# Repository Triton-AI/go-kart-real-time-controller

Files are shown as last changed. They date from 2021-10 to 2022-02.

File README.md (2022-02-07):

# Go-Kart Real-Time Controller



## Navigation

This repository is organized as follows:

- `ROS2` contains the gokart packet library and ROS2 driver
- `PCB` contains Altium PCB design files
- `MCU` contains microcontroller codes ([depricated, moved to a separate repository](https://github.com/Triton-AI/go-kart-real-time-controller-mbed))

## Documentations

- [Getting started with packet communication library](ROS2/src/tai_gokart_packet/design/README.md)
- [Packet API documentation](ROS2/src/tai_gokart_packet/design/Packet_API.md)

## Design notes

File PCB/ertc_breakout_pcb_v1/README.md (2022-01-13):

# V1 Errors
NUCLEO Connectors (J1, J2) flipped pinout

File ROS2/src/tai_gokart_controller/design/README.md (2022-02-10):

# Go Kart Controller - ROS2 Driver

## Purpose of Package

This packet is a ROS2 driver for Triton AI's go-kart real-time controller. The current development work targets ROS2 Galactic.

The packet is capable of sending control messages and receive sensor and state report from the controller.

## API

## Inner Working

The packet assumes the following state machine exists on the MCU. See a detailed explanation in the [MCU code repository](https://github.com/Triton-AI/go-kart-real-time-controller-mbed).

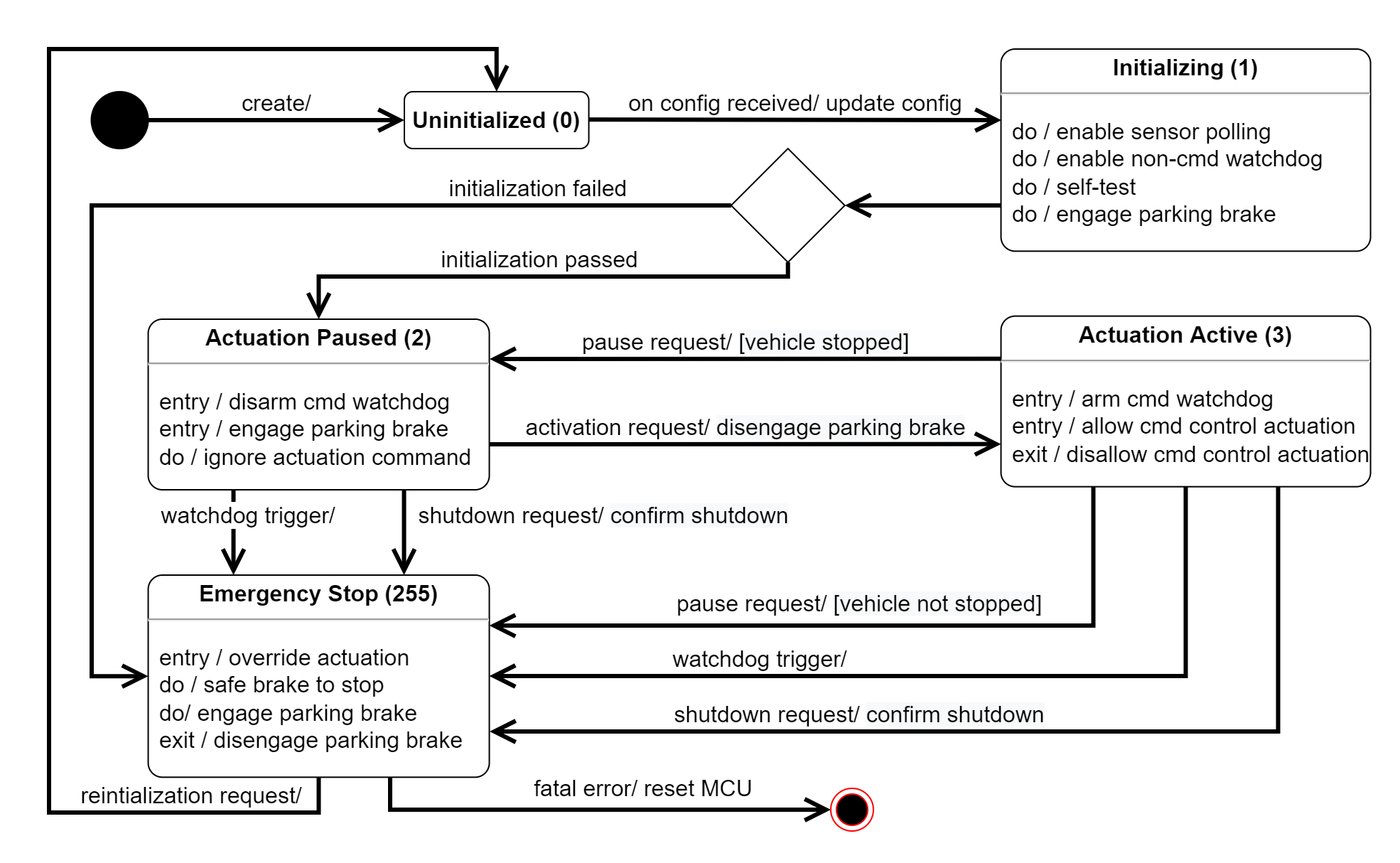
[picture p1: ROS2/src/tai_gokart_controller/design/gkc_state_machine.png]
GKC State Machine


The state machine proposal is purposefully made close to [ROS2 Lifecycle](https://design.ros2.org/articles/node_lifecycle.html) to enable easier management, with the major difference being an additional "emergency stop" state. Since ROS2 Lifecycle system does not support custom state, it is implemented as part of the uninitialized state in ROS2 Lifecycle, while the error state is used to direct all emergency stop requests to the uninitialized state.

Another difference is in the shutdown procedure where shutdown transition will always eventually end in emergency stop state (by signaling transition error and be directed to uninitialized state). The rationale is that the software should always have control or communication with the vehicle as much as possible, instead of destructing such interface. Only fatal error or user interrupt can destruct the node.

## Known Issues

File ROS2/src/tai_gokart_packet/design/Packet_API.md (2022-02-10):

# Packet API

## Introduction

The transfer of messages through network interfaces of the team's choice (Serial, CAN, Ethernet) follows a standardized packet API for message serialization (encoding) and deserialization (decoding).

The low-level communication interface (LLCI) of Serial, CAN and Ethernet is agnostic about what is being transferred. On top of that, the high-level communication interface (HLCI), which is mainly the packet factory, is responsible for encoding and decoding between C++ class representation of message and low-level buffer to/from LLCI.

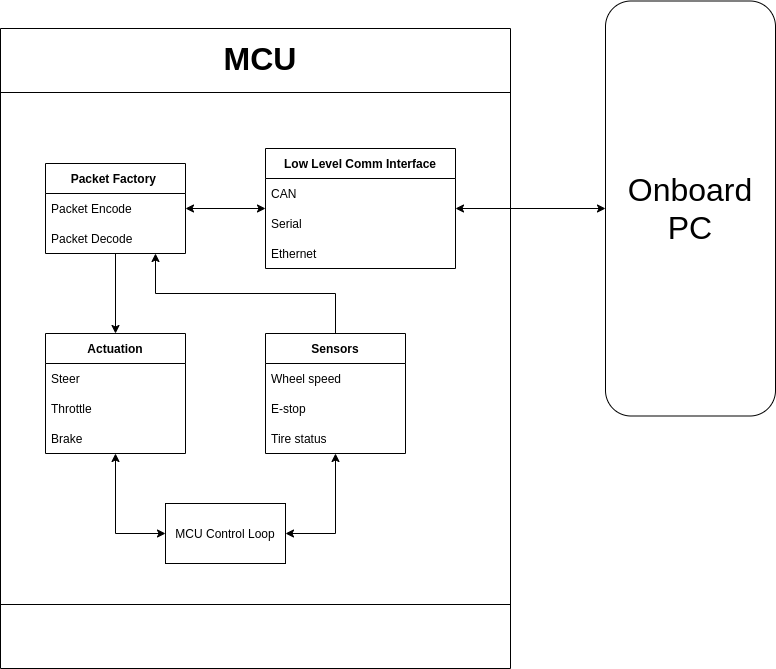
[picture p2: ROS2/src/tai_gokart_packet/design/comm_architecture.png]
Communication Architecture


There are packet factories on both sides of the communication system, making it a reusable common library for both Go-Kart Controller (GKC) software and high-level softwares (ROS2).

## Packet Basics

Each packet is a variable buffer of bytes.

The Packet API takes substantial reference from VESC packet API.

A standard packet begins with byte 0x02, followed by 1 byte of payload length. Payload cannot exceed 256 bytes. After that, 2 bytes are used for payload checksum, and finally there is one termination byte 0x03.

The **first byte (FB)** of each payload type is uniquely identifiable.

Extended packet is not needed and not implemented at the moment, but any LLCI implementation should not rule out the possibility of such packet in the future.

To avoid garbage data, unused payload buffer section should be initiated to 0x00. 0x00 cannot have any substaintial meaning in the playload other than data.

## Core Payloads

These messages concerns the basic communication and device control, such as communication establishment, firmware version, MCU reset, heartbeat, and watchdog.

### Handshake \#1

Payload size: 5 Byte

FB: 0x04

The first handshake is initiated by the PC. The first byte of the payload is 0x04, followed by a 4-byte randomly generated unsigned integer as the sequence number.

### Handshake \#2

Payload size: 5 Byte

FB: 0x05

The second handshake given by the MCU after hearing handshake #1 from the PC. The first byte of the payload is 0x05, followed by a 4-byte unsigned integer which is the bit-wise complement of the number in handshake #1.

### Request Firmware Version

Payload size: 1 Byte

FB: 0x06

The PC requesting firmware version from the MCU.

### Respond Firmware Version

Payload size: 4 Byte

FB: 0x07

The MCU's response of firmware version in three `uint8`: version `x.y.z`

### Reset MCU

Payload size: 5 Byte

FB: 0xFF

The PC commanding a MCU reset. the four bytes of the message contains alternating 1s and 0s (decimal 2863311530 or hex AAAAAAAA).

### Heartbeat

Payload size: 3 Byte

FB: 0xAA

Bidirectional message with a `uint8` rolling counter that increments or overflows with every message sent to the other side, as well as a `uint8` state code of the MCU state machine state, which is only sent by MCU.

### Log

Payload size: variable

FB: 0xAD

String log with severity level of info, warning, error or fatal. The `c_str` content of the string cannot exceed 253 byte. The response to different severity levels is implementation-dependant.

## Configuration Payloads

These messages set the configurations of the controller.

### Configuation

Payload size: 49 Byte

FB: 0xA0

The PC sends configuations to the MCU, containing actuation calibrations and watchdog timeout intervals.

## Control Payloads

### Control

Payload size: 13 Byte

FB: 0xAB

The PC commands steering, throttle, and brake to the MCU.

### State Transition

Payload size: 2 Byte

FB: 0xA1

The PC requests a state transition on the MCU. Possible states include unintialized, initialized, active, paused, and emergency stop.

### Shutdown \#1

Payload size: 5 Byte

FB: 0xA2

The PC requests a shutdown to the MCU. The message contains a sequence number.

### Shutdown \#2

Payload size: 5 Byte

FB: 0xA3

The MCU responds to the shutdown command from the computer by adding one to the incoming sequence number in Shutdown #1.

## Feedback Payloads

### Sensors

These messages request or send GKC state, and sensor feedbacks.

Payload size: 48 Byte

FB: 0xAC

The MCU sends sensor data to the PC, containing wheel speeds, pressures, voltage, etc., and sensor fault flags.

## Reference

| Description | Payload size | Payload FB | Data Structure | Sender |
|---|---|---|---|---|
| Handshake #1 | 5 | 0x04 | uint32 sequence number. | PC |
| Handshake #2 | 5 | 0x05 | uint32 sequence number | MCU |
| Request Firmware Version | 1 | 0x06 | | PC |
| Respond Firmware Version | 4 | 0x07 | 3 * uint8 version number | MCU |
| Reset MCU | 5 | 0xFF | uint32 magic number | PC |
| Heartbeat | 2 | 0xAA | uint8 rolling counter | Both |
| Log | Variable | 0xAD | severity and string content | Both |
| Configuration | 49 | 0xA0 | a packed struct of configurables | PC |
| Control | 13 | 0xAB | throttle, steering, and brake | PC |
| State Transition | 2 | 0xA1 | uint8 state number | PC |
| Sensors | 22 | 0xAC | a packed struct of sensor readings | MCU |
| Shutdown \#1 | 5 | 0xA2 | uint32 sequence number. | PC |
| Shutdown \#2 | 5 | 0xA3 | uint32 sequence number. | MCU |

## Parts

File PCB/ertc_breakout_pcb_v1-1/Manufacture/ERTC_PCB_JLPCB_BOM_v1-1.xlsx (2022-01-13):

Part Number | Description | Designator | Footprint | Manufacturer 1 | Manufacturer Part Number 1 | Supplier 1 | Supplier Part Number 1 | Quantity | Comment
CGA3E2X7R1H472K080AA | CAP CER 4700PF 50V X7R 0603 | C1, C3 | CAP 0603_1608 |  |  | DigiKey | 445-5661-1-ND | 2
CL10B104KA8NNNC | CAP CER 0.1UF 25V X7R 0603 | C2, C4, C5, C6, C7, C8, C9 | CAP 0603_1608 |  |  | DigiKey | 1276-1006-1-ND | 7
LTST-C170GKT | LED GREEN CLEAR SMD | D1 | LED 0805_2012 GREEN |  |  | DigiKey | 160-1179-1-ND | 1
SSW-135-01-T-D |  | J1, J2 | SAMTEC_SSW-135-03-G-D |  |  |  |  | 2 | DNP
A-DF_09_A/KG-T2S | 9 Position D-Sub Receptacle, Female Sockets Connector | J3, J4, J7 | ASSMANN_A-DF09A/KG-T2S |  |  |  |  | 3 | DNP
39-30-1039 | Connector Header Through Hole 3 position 0.165 _4.20mm_ | J5, J6, J8, J9, J11, J12, J13, J14, J15, J16, J17, J18, J19, J20, J23, J24, J25 | MOLEX_39-30-1039 |  |  |  |  | 17 | DNP
0039281063 | Connector Header Through Hole, 6 position 0.165 (4.20mm) | J10, J21, J22 | MOLEX_0039281063 |  |  |  |  | 3 | DNP
0039301049 | Connector Header Through Hole 4 position 0.165 _4.20mm_ | J26, J27, J28, J29, J30, J32, J33, J34, J35, J36 | MOLEX_0039301049 |  |  |  |  | 10 | DNP
XT30UPB-M | Plug; DC supply; XT30; male; PIN: 2; for cable; soldered; 30A; 500V | J31 | AMASS_XT30-M |  |  |  |  | 1 | DNP
RNCP0805FTD1K00 | RES 1K OHM 1% 1/4W 0805 | R1, R3, R5, R7 | RES 0805_2012 |  |  | DigiKey | RNCP0805FTD1K00CT-ND | 4 | DNP
RMCF0603FT60R4 | RES 60.4 OHM 1% 1/10W 0603 | R2, R4, R6, R8 | RES 0603_1608 |  |  | DigiKey | RMCF0603FT60R4CT-ND | 4
CRCW06030000Z0EBC | RES SMD 0 OHM JUMP 1/10W 0603 | R9, R11, R12, R13, R14, R15, R16, R17, R18 | RES 0603_1608 |  |  | DigiKey | 541-4013-1-ND | 9 | DNP
CRGCQ0603F1K2 | CRGCQ 0603 1K2 1% | R10 | RES 0603_1608 |  |  | DigiKey | A129689CT-ND | 1
SN65HVD230DR | 3.3 V CAN Transceiver with Standby Mode 8-SOIC -40 to 85 | U1, U2 | SOIC127P599X175-8N |  |  |  |  | 2
MAX3232IDR | 3-V to 5.5-V multichannel RS-232 line driver & receiver 16-SOIC -40 to 85 | U3 | SOIC127P600X175-16N |  |  |  |  | 1

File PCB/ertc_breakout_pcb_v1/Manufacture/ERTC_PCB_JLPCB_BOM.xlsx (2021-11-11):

Part Number | Description | Designator | Footprint | Manufacturer | Manufacturer Part Number 1 | Supplier 1 | Supplier Part Number 1 | Quantity | Comment
CL10B472JB8NNNC | X7R 4.7nF ±5% 50V 0603 Multilayer Ceramic Capacitors MLCC - SMD/SMT ROHS | C1, C3 | CAP 0603_1608 | Murata Electronics |  |  |  | 2
CL10B104JB8NNNC | X7R 100nF ±5% 50V 0603 Multilayer Ceramic Capacitors MLCC - SMD/SMT ROHS | C2, C4, C5, C6, C7, C8, C9 | CAP 0603_1608 | Samsung Electro-Mechanics |  |  |  | 7
LTST-C170GKT | LED GREEN CLEAR SMD | D1 | LED 0805_2012 GREEN | Lite-On Inc. |  | DigiKey | 160-1179-1-ND | 1
SSW-135-01-T-D |  | J1, J2 | SAMTEC_SSW-135-01-T-D | Samtec |  |  |  | 2 | DNP
A-DF_09_A/KG-T2S | 9 Position D-Sub Receptacle, Female Sockets Connector | J3, J4, J7 | ASSMANN_A-DF09A/KG-T2S | Assmann WSW Components |  | Digikey | AE10921-ND | 3 | DNP
39-30-1039 | Connector Header Through Hole 3 position 0.165 _4.20mm_ | J5, J6, J8, J9, J11, J12, J13, J14, J15, J16, J17, J18, J19, J20, J21, J22, J23, J24, J25 | MOLEX_39-30-1039 |  |  |  |  | 19 | DNP
0039281063 | Connector Header Through Hole, 6 position 0.165 (4.20mm) | J10 | MOLEX_0039281063 |  |  |  |  | 1 | DNP
0039301049 | Connector Header Through Hole 4 position 0.165 _4.20mm_ | J26, J27, J28, J29, J30, J32, J33, J34, J35, J36 | MOLEX_0039301049 |  |  |  |  | 10 | DNP
XT30UPB-M | Plug; DC supply; XT60; male; PIN: 2; for cable; soldered; 30A; 500V | J31 | AMASS_XT30-M |  |  |  |  | 1 | DNP
RNCP0805FTD1K00 | 250mW ±1% ±25ppm/℃ 1kΩ - 0805 Chip Resistor - Surface Mount ROHS | R1, R3, R5, R7 | RES 0805_2012 | UNI-ROYAL(Uniroyal Elec) |  |  |  | 4 | DNP
0603WAF604JT5E | 60.4Ω ±1% ±100ppm/℃ 0.1W 0603 Chip Resistor - Surface Mount ROHS | R2, R4, R6, R8 | RES 0603_1608 | UNI-ROYAL(Uniroyal Elec) |  |  |  | 4
CRCW06030000Z0EBC | RES SMD 0 OHM JUMP 1/10W 0603 | R9 | RES 0603_1608 | Vishay Dale |  | DigiKey | 541-4013-1-ND | 1 | DNP
0603WAJ0122T5E | 1.2kΩ ±5% ±100ppm/℃ 0.1W 0603 Chip Resistor - Surface Mount ROHS | R10 | RES 0603_1608 | UNI-ROYAL(Uniroyal Elec) |  |  |  | 1
SN65HVD230DR | 3.3 V CAN Transceiver with Standby Mode 8-SOIC -40 to 85 | U1, U2 | SOIC127P599X175-8N | Texas Instruments |  | DigiKey | 296-11654-2-ND | 2
MAX3232IDR | 3-V to 5.5-V multichannel RS-232 line driver & receiver 16-SOIC -40 to 85 | U3 | SOIC127P600X175-16N | Texas Instruments |  | DigiKey | 296-13098-2-ND | 1

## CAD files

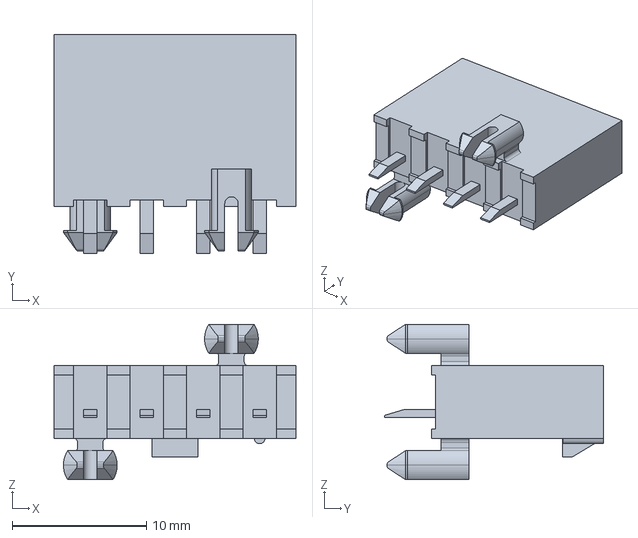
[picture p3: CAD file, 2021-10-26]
PCB/ertc_breakout_pcb_v1-1/CAD Models/0039301049/39-30-1049.stp
18.0 x 16.3 x 11.6 mm

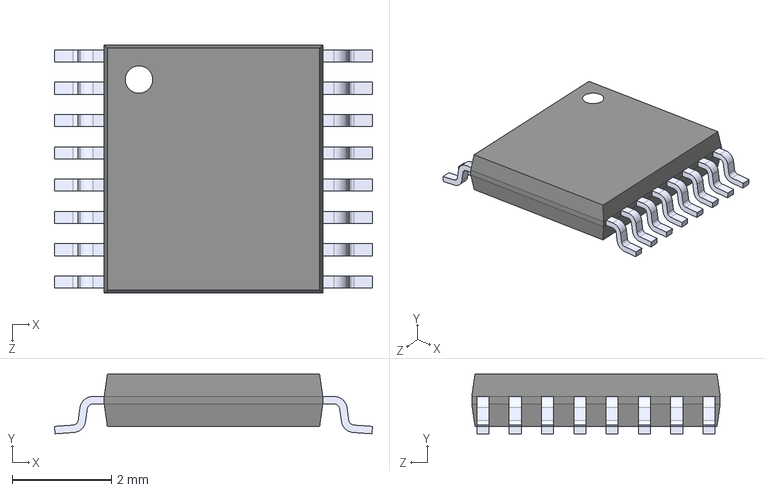
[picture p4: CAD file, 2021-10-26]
PCB/ertc_breakout_pcb_v1-1/CAD Models/MAX3221EIPWR/MAX3221EIPWR.STEP
6.40 x 1.20 x 5.00 mm

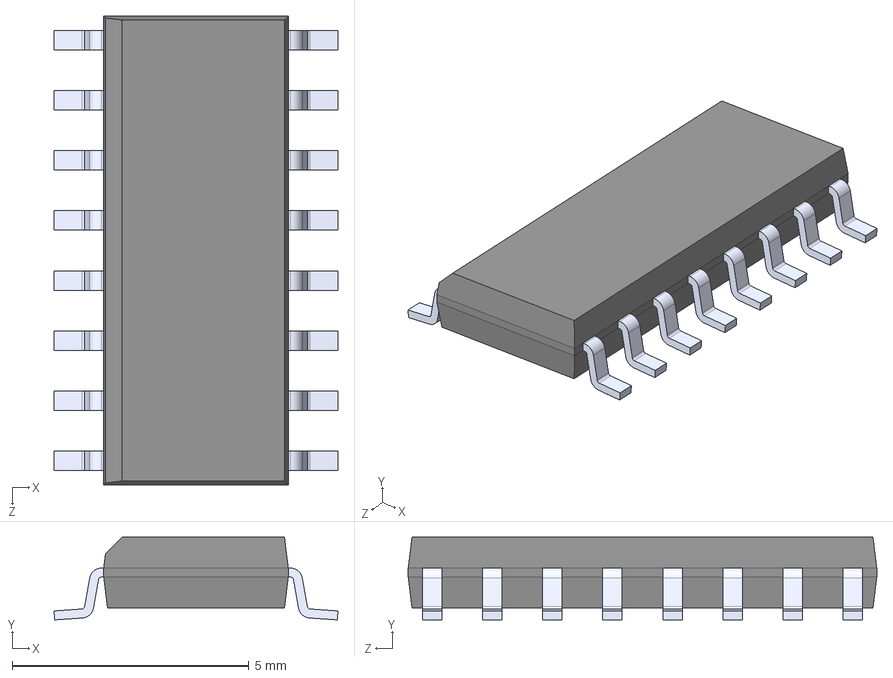
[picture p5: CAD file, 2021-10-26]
PCB/ertc_breakout_pcb_v1-1/CAD Models/MAX3232IDR/MAX3232IDR.STEP
6.00 x 1.75 x 9.90 mm

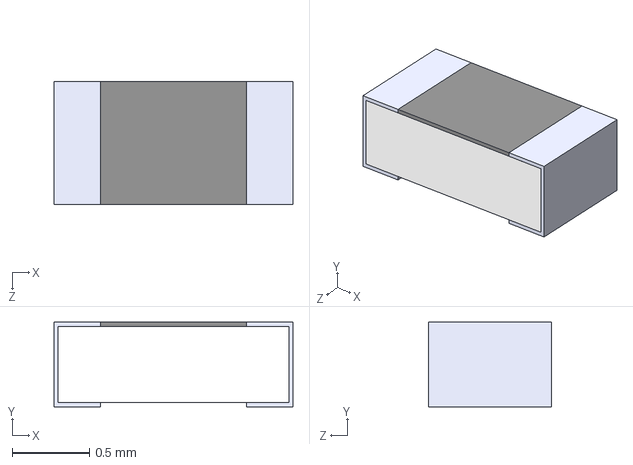
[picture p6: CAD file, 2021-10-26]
PCB/ertc_breakout_pcb_v1-1/CAD Models/RMCF0603FT60R4/RMCF0603FT60R4.STEP
1.55 x 0.55 x 0.8 mm

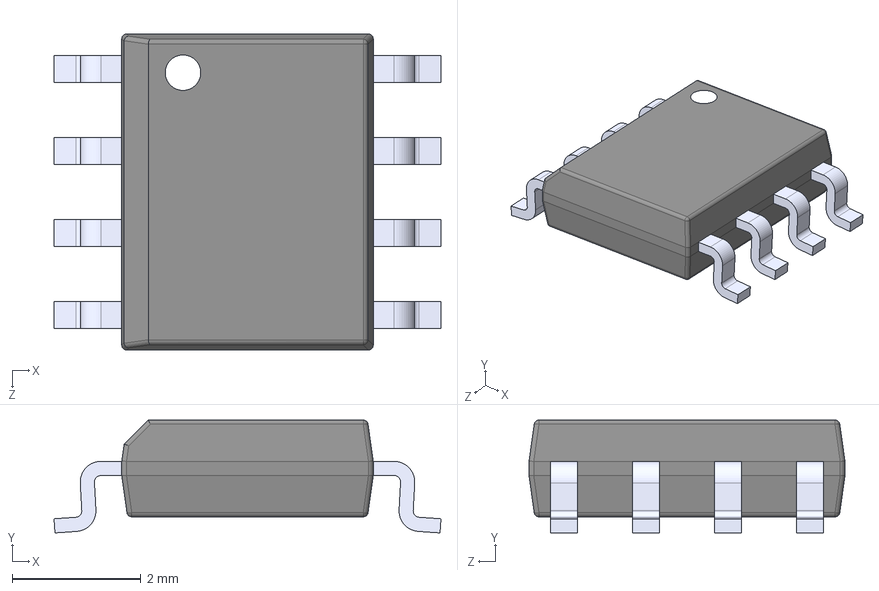
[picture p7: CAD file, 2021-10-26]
PCB/ertc_breakout_pcb_v1-1/CAD Models/SN65HVD230DR/SN65HVD230DR.STEP
6.00 x 1.75 x 4.90 mm

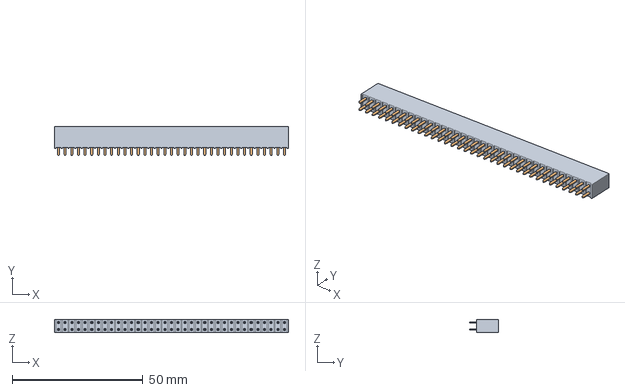
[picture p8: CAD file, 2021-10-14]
PCB/ertc_breakout_pcb_v1-1/CAD Models/SSW-135-01-T-D/SSW-135-01-T-D.stp
89.4 x 11.2 x 4.95 mm
_T1SSW-135-01-T-D
_P2SSW-135-01-T-D

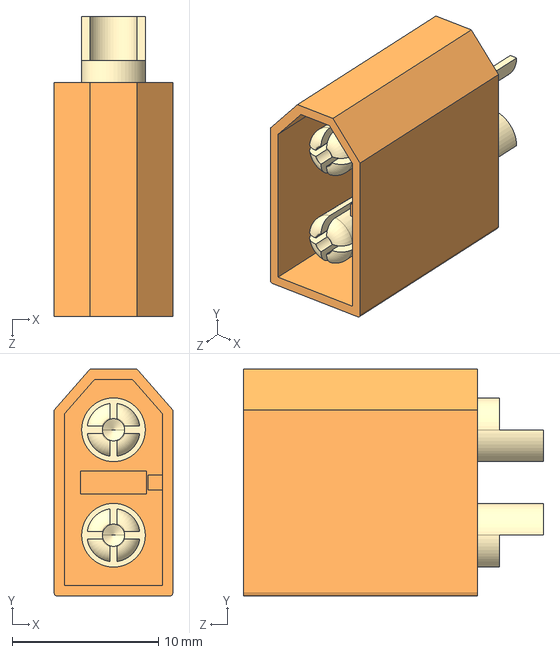
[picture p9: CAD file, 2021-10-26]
PCB/ertc_breakout_pcb_v1-1/CAD Models/XT60-M/XT60-M--3DModel-STEP-56544.STEP
8.10 x 15.5 x 20.5 mm

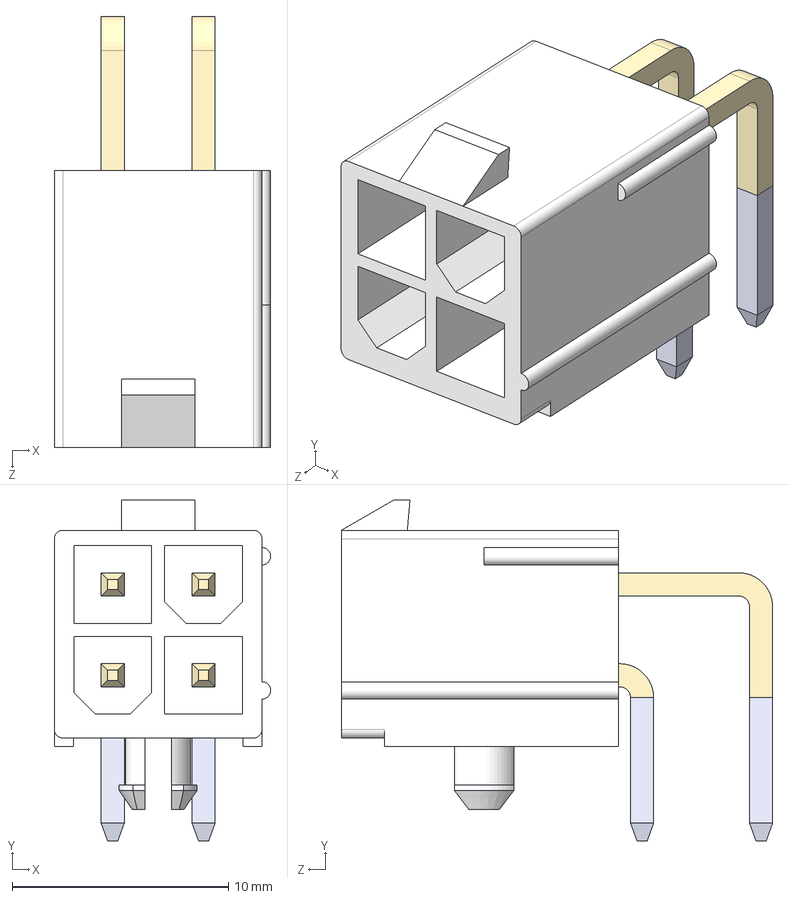
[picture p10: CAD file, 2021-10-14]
PCB/ertc_breakout_pcb_v1-1/CAD Models/0026013115/0026013115--3DModel-STEP-56544.STEP
10.0 x 15.8 x 19.9 mm

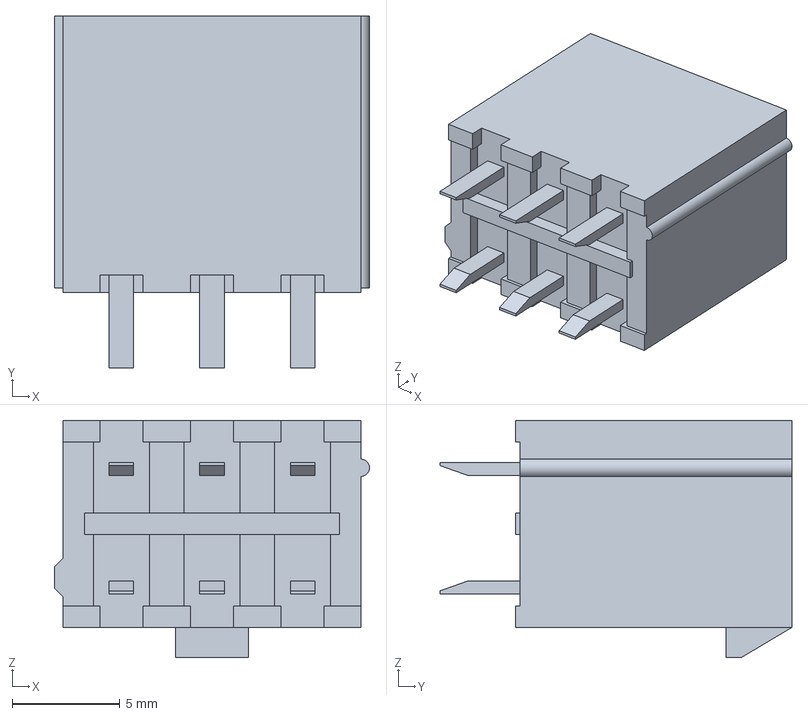
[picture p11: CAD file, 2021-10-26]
PCB/ertc_breakout_pcb_v1-1/CAD Models/0039281063/39281063--3DModel-STEP-390490.STEP
14.6 x 16.3 x 11.0 mm

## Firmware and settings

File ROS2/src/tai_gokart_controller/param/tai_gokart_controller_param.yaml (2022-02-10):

/**:
  ros__parameters:
    # node
    sensor_pub_hz: 100

    # comm interface
    comm_type: 'serial' # serial, ethernet, can
    serial:
      port: '/dev/ttyACM0'
      baud_rate: 115200

    # steering config (refers to average front wheel angle in radian)
    max_steering_left: 0.524  # (left +, righ -)
    max_steering_right: -0.524  # (left +, righ -)
    neutral_steering: 0.0  # should be between max and min

    # throttle config (unit is implementation-dependant, typically unit-less out of 1.0)
    max_throttle: 1.0
    min_throttle: 0.1
    zero_throttle: 0.0  # should be smaller than min

    # brake config (in psi)
    max_brake: 2000.0
    min_brake: 200.0
    zero_brake: 0.0  # should be smaller than min

    # watchdog timeouts (in millisecond)
    control_timeout_ms: 100  # timeout for control packets
    comm_timeout_ms: 100  # timeout for heartbeat packets
    sensor_timeout_ms: 100  # timeout between two sensor pollings

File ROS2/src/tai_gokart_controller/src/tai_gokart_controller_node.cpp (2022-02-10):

/**
 * @file tai_gokart_controller_node.cpp
 * @author Haoru Xue (haoru.xue@autoware.org)
 * @brief
 * @version 0.1
 * @date 2022-02-07
 *
 * @copyright Copyright 2022 Triton AI
 *
 */
#include <string>
#include <memory>

#include "tai_gokart_controller/tai_gokart_controller_node.hpp"

namespace tritonai
{
namespace gkc
{
using std::placeholders::_1;

GkcNode::GkcNode(const rclcpp::NodeOptions & options)
: rclcpp_lifecycle::LifecycleNode("gkc_node", options)
{
  configs_ = ConfigList{
    Config{"comm_type", Configurable(declare_parameter<std::string>("comm_type", "serial"))},
    Config{"serial_port",
      Configurable(declare_parameter<std::string>("serial.port", "/dev/ttyACM0"))},
    Config{"baud_rate", Configurable(declare_parameter<int64_t>("serial.baud_rate", 115200))},
  };
  interface_ = std::make_unique<GkcInterface>(configs_);
}

LifecycleNodeInterface::CallbackReturn GkcNode::on_configure(
  const rclcpp_lifecycle::State &)
{
  // If in emergency mode, bring out of emergency
  if (interface_ && interface_->get_state() == GkcLifecycle::Emergency) {
    static constexpr uint32_t RELEASE_ESTOP_PAUSE_S = 5;
    static constexpr uint32_t RELEASE_ESTOP_WAIT_MS = 100;
    RCLCPP_WARN(get_logger(), "Attempting to remove emergency state.");
    RCLCPP_WARN(get_logger(), "!!! BRAKE WILL BE REMOVED IN %d SECOND !!!", RELEASE_ESTOP_PAUSE_S);
    std::this_thread::sleep_for(std::chrono::seconds(RELEASE_ESTOP_PAUSE_S));
    RCLCPP_WARN(get_logger(), "Requesting to remove emergency state.");
    if (interface_->release_emergency_stop(RELEASE_ESTOP_WAIT_MS)) {
      RCLCPP_WARN(get_logger(), "Success. Emergency state removed.");
      RCLCPP_WARN(get_logger(), "!!! BRAKE IS REMOVED !!!");
      RCLCPP_INFO(
        get_logger(),
        "Please ignore Lifecycle transition failure. The vehicle is now in uninitialized state.");
    } else {
      RCLCPP_ERROR(get_logger(), "Failed. Vehicle still in emergency state. Brake still on.");
    }
    dump_logs();
    return LifecycleNodeInterface::CallbackReturn::FAILURE;
  }

  // If going through normal initialization
  static bool first_time = true;
  static auto pkt = ConfigGkcPacket();
  if (first_time) {
    double sensor_pub_interval = 1.0 / declare_parameter<int32_t>("sensor_pub_hz", 100);
    state_pub_ = create_publisher<GkcState>("gkc_state", rclcpp::QoS{10});
    cmd_sub_ =
      create_subscription<GkcCommand>(
      "gkc_cmd", rclcpp::QoS{10},
      std::bind(&GkcNode::cmd_callback, this, _1));
    state_pub_timer_ = create_timer(
      this, get_clock(), rclcpp::duration<float>(sensor_pub_interval), [this] {
        state_pub_timer_callback();
      });
    pkt.values.max_steering_left = declare_parameter<float>("max_steering_left", 0.524);
    pkt.values.max_steering_right = declare_parameter<float>("max_steering_right", -0.524);
    pkt.values.neutral_steering = declare_parameter<float>("neutral_steering", 0.0);
    pkt.values.max_throttle = declare_parameter<float>("max_throttle", 1.0);
    pkt.values.min_throttle = declare_parameter<float>("min_throttle", 0.1);
    pkt.values.zero_throttle = declare_parameter<float>("zero_throttle", 0.0);
    pkt.values.max_brake = declare_parameter<float>("max_brake", 2000.0);
    pkt.values.min_brake = declare_parameter<float>("min_brake", 200.0);
    pkt.values.zero_brake = declare_parameter<float>("zero_brake", 0.0);
    pkt.values.control_timeout_ms = declare_parameter<int64_t>("control_timeout_ms", 100);
    pkt.values.comm_timeout_ms = declare_parameter<int64_t>("comm_timeout_ms", 100);
    pkt.values.sensor_timeout_ms = declare_parameter<int64_t>("sensor_timeout_ms", 100);
    first_time = false;
  }
  RCLCPP_INFO(get_logger(), "Sending configuration to the MCU.");
  static constexpr uint32_t CONFIGURE_WAIT_MS = 100;
  static constexpr uint32_t MAX_INITIALIZE_WAIT_S = 60;
  if (interface_->initialize(pkt, CONFIGURE_WAIT_MS)) {
    RCLCPP_INFO(
      get_logger(), "MCU is initializing. Waiting for a max of %d second before timeout...",
      MAX_INITIALIZE_WAIT_S);
    auto start_time = get_clock()->now();
    while ((get_clock()->now() - start_time).seconds() < MAX_INITIALIZE_WAIT_S) {
      if (interface_->get_state() == GkcLifecycle::Inactive) {
        RCLCPP_INFO(get_logger(), "MCU is initialized and in inactive state.");
        dump_logs();
        return LifecycleNodeInterface::CallbackReturn::SUCCESS;
      }
      std::this_thread::sleep_for(std::chrono::duration<double>(1.0));
    }
    RCLCPP_ERROR(get_logger(), "MCU initialization timeout.");
  } else {
    RCLCPP_ERROR(get_logger(), "Failed to send configuration to the MCU.");
  }
  dump_logs();
  return LifecycleNodeInterface::CallbackReturn::FAILURE;
}

LifecycleNodeInterface::CallbackReturn GkcNode::on_activate(
  const rclcpp_lifecycle::State &)
{
  static constexpr uint32_t WAIT_MS = 100;
  if (interface_->activate(WAIT_MS)) {
    RCLCPP_WARN(get_logger(), "!!! VEHICLE IS ALIVE !!!");
    return LifecycleNodeInterface::CallbackReturn::SUCCESS;
  } else {
    RCLCPP_WARN(get_logger(), "Failed to activate vehicle. Maybe in emergency stop?");
    return LifecycleNodeInterface::CallbackReturn::FAILURE;
  }
}

LifecycleNodeInterface::CallbackReturn GkcNode::on_deactivate(
  const rclcpp_lifecycle::State &)
{
  static constexpr uint32_t WAIT_MS = 100;
  if (interface_->activate(WAIT_MS)) {
    RCLCPP_WARN(get_logger(), "VEHICLE IS PAUSED");
    return LifecycleNodeInterface::CallbackReturn::SUCCESS;
  } else {
    RCLCPP_WARN(
      get_logger(),
      "!!! VEHICLE STILL ALIVE !!! Failed to pause vehicle. This may cause emergency stop.");
    return LifecycleNodeInterface::CallbackReturn::FAILURE;
  }
}

LifecycleNodeInterface::CallbackReturn GkcNode::on_cleanup(
  const rclcpp_lifecycle::State &)
{
  static constexpr uint32_t WAIT_MS = 100;
  RCLCPP_INFO(get_logger(), "Attempting to bring the vehicle out of emergency mode.");
  if (interface_->release_emergency_stop(WAIT_MS)) {
    RCLCPP_INFO(get_logger(), "Done. Vehicle is now in uninitialized state.");
    return LifecycleNodeInterface::CallbackReturn::SUCCESS;
  } else {
    RCLCPP_INFO(get_logger(), "Failed. Vehicle is still in emergency mode.");
    return LifecycleNodeInterface::CallbackReturn::FAILURE;
  }
}

LifecycleNodeInterface::CallbackReturn GkcNode::on_shutdown(
  const rclcpp_lifecycle::State &)
{
  static constexpr uint32_t WAIT_MS = 100;
  if (interface_->shutdown(WAIT_MS)) {
    RCLCPP_INFO(get_logger(), "Vehicle shutdown.");
    return LifecycleNodeInterface::CallbackReturn::SUCCESS;
  } else {
    RCLCPP_INFO(get_logger(), "Vehicle failed to shutdown. It should now go to emergency mode.");
    return LifecycleNodeInterface::CallbackReturn::FAILURE;
  }
}
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

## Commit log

2021-10-14 Created Altium project, added connectors to PCB
    [0026013115--3DModel-STEP-56544.STEP, 0026013115.SchLib, A-DF_09_A_KG-T2S.SchLib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]
2021-10-14 drop ignored files from git
    [SAMTEC_SSW-135-01-T-D.PcbLib, SSW-135-01-T-D.SchLib]
2021-10-21 Changed connectors: right angle to vertical. power to xt30, 6pin for encoder
    [39-30-1049.stp, 39281063--3DModel-STEP-390490.STEP, SnapEDApcb.PcbLib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]
2021-10-25 Added NUCLEO connetions, CAN transceiver, UART to RS232
    [MAX3221EIPWR.STEP, MAX3221EIPWR.SchLib, RESC1508X55N.PcbLib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]
2021-10-26 Terminated CAN1 and CAN2
    [connectors.SchDoc]
2021-10-26 Added UART to RS232 converter
    [MAX3232IDR.STEP, MAX3232IDR.SchLib, SOIC127P600X175-16N.PcbLib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]
2021-10-29 Wired schematic
    [connectors (1).SchDoc, connectors.SchDoc, connectors1.0.SchDoc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]
2021-10-29 routed CAN and UART-RS232
    [connectors.SchDoc, ertc_breakout_pcb.PcbDoc, ertc_breakout_pcb.PrjPcb]
2021-10-29 Relabel Used Pins
    [connectors (1).SchDoc]
2021-10-30 Roger: wire pins to connectors, Ryan: clean up schematic
    [connectors.SchDoc, ertc_breakout_pcb.PcbDoc, ertc_breakout_pcb.PrjPcb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]
2021-10-30 Routed PCB v1
    [connectors.SchDoc, ertc_breakout_pcb.PcbDoc, ertc_breakout_pcb.PrjPcb]
2021-11-04 Resized PCB
    [connectors.SchDoc, ertc_breakout_pcb.PcbDoc, ertc_breakout_pcb.PrjPcb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]
2021-11-05 resized PCB again
    [ertc_breakout_pcb.PcbDoc]
2021-11-05 Placed power LED on PCB, minor changes to PCB routing
    [connectors (1).SchDoc, connectors.SchDoc, connectors1.0.SchDoc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]
2021-11-11 Generated gerbers, NC drills, pick and place, and BOM for JLCPCB
    [ERTC_PCB_JLPCB_BOM.xlsx]
2021-11-11 Updated gerbers with board outline
    [ertc_breakout_pcb.PcbDoc, ertc_breakout_pcb.PrjPcb]
2021-11-11 Updated JLC PCB BOM
    [ERTC_PCB_JLPCB_BOM.xlsx]
2021-11-11 Increase pad size for ICs
    [ertc_breakout_pcb.PcbDoc, ertc_breakout_pcb.PrjPcb]
2021-12-09 PCB v1.1, fixed NUCLEO pinout, added 2 more connectors for encoder
    [0026013115--3DModel-STEP-56544.STEP, 0026013115.SchLib, 39-30-1049.stp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]
2021-12-17 Updated V1.1 BOM
    [ERTC_PCB_JLPCB_BOM_v1-1.xlsx, ERTC_PCB_JLPCB_BOM_v1.xlsx]
2022-02-07 populate launch file and param file
    [tai_gokart_controller_param.yaml]
2022-02-07 add serial driver to gkc dependencies
2022-02-07 add serial param
    [tai_gokart_controller_param.yaml]
2022-02-09 wip controller node
    [tai_gokart_controller_param.yaml]

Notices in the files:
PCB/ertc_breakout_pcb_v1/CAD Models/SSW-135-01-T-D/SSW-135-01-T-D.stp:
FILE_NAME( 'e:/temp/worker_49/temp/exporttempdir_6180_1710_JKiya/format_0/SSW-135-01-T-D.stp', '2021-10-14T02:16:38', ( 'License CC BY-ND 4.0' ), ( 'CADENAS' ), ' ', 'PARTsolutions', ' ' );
